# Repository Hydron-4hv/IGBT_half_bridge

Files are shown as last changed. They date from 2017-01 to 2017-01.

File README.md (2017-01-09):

# IGBT_half_bridge
PCB for general use of TO-247 IGBTs in half bridge configuration. Variants for parallel IGBTs and horizontal mounting

Design notes:
- Have included a lot of different holes for various mounting requirements, so looks a bit swiss-cheesed
- Should be able to trim off part of the board and still access Vbus+/- and bridge output nodes
- Electrolytic cap footprints should be able to accommodate up to 35mm dia. caps, though with a little bit hanging over the edge of the PCB
- Various Fischer Elektronik SK 481 heatsinks can be used (with clips to hold IGBTs), either 2 separate heatsinks (suggest 37.5mm length) to avoid isolation requirements, or larger 50-84mm with isolation pads behind IGBTs. In all cases use an insulated washer for heatsink mounting screw, and consider adding kapton tape or similar to top layer to add isolation between heatsink and top layer tracks.
- Other heatsinks with IGBTs either vertical or horizontal (under PCB mount, screws accessed via supplied holes) can be used as desired 

Output notes:
- 3 different "PCB Variants" have been defined and output files generated:
  - Single IGBT in each of upper and lower half bridge position, SMD gate resistor, 2x 37.5mm SK481 heatsinks, no electrolytic caps
  - Dual IGBTs in each of upper and lower half bridge position, THD gate resistor, 2x 37.5mm SK481 heatsinks, electrolytic caps fitted
  - Dual IGBTs in each of upper and lower half bridge position (horizontally mounted), THD gate resistor, no heatsink, electrolytic caps fitted
- The "schematic" PDFs include a 3D model for viewing in compatible software (Adobe reader works, Foxit does not, unsure about others)

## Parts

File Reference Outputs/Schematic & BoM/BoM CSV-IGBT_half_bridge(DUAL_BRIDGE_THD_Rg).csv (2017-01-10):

Designator | Value | Description | Fitted | Footprint | LibRef | Quantity
C1 | 5uF 800V | Capacitor | Fitted | B32774 5uF 800V | Cap | 1
C2, C3 | 390uF | WCAP-AIG8 Aluminum Electrolytic Capacitors, 390uF | Fitted | WCAP-AIG8_30x46 | WCAP-AIG8, 861011485019 | 2
C4, C5, C6, C7, C8, HS1, HS2 |  |  | Fitted | 2220C, 1812C, 2220C, 1812C, Cap_multi_footprint, SK 481 37.5, SK 481 37.5_FLIP | Capacitor, Capacitor, Capacitor, Capacitor, Capacitor, SK_481_37.5, SK_481_37.5 | 7
D1, D3, D5, D7 |  | SS26 Schottky rectifier | Fitted | DO-214AA_(SMB-J-BEND)_UNI | SS26 | 4
D2, D4, D6, D8 |  | WE-TVSP Power TVS Diode, bidirectional, 600 W, 24 VDC | Fitted | DO-214AA_Bidirectional | WE-TVSP DO-214AA, 824521241 | 4
J1 |  | WR-BHD 2.54mm Male Box Header | Fitted | 61202021621 | 61202021621 | 1
L1, L2, L3, L4 | 32O | WE-CBF SMD EMI Suppression Ferrite Bead, 1206, 32O | Fitted | WE-CBF_1206_High Speed | WE-CBF, 7427921 | 4
Q1, Q2, Q3, Q4 |  | IGBT, TO-247, Vertical | Fitted | TO-247 | TO-247_IGBT_V | 4
R1, R2, R13, R18 | 3R3 2W | Resistor | Fitted | Res_Radial_2W | Res2 | 4
R3, R4, R7, R8, R11, R12, R16, R17 | 5R6 1W | Resistor | Not Fitted | RES_2512 | Res2 | 0

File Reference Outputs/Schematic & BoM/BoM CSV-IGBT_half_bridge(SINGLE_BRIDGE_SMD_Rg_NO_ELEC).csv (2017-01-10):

Designator | Value | Description | Fitted | Footprint | LibRef | Quantity
C1 | 5uF 800V | Capacitor | Fitted | B32774 5uF 800V | Cap | 1
C2, C3 | 390uF | WCAP-AIG8 Aluminum Electrolytic Capacitors, 390uF | Not Fitted | WCAP-AIG8_30x46 | WCAP-AIG8, 861011485019 | 0
C4, C6, HS1, HS2 |  |  | Fitted | 2220C, 2220C, SK 481 37.5, SK 481 37.5_FLIP | Capacitor, Capacitor, SK_481_37.5, SK_481_37.5 | 4
C5, C7, C8 |  |  | Not Fitted | 1812C, 1812C, Cap_multi_footprint | Capacitor | 0
D1, D3 |  | SS26 Schottky rectifier | Fitted | DO-214AA_(SMB-J-BEND)_UNI | SS26 | 2
D2, D4 |  | WE-TVSP Power TVS Diode, bidirectional, 600 W, 24 VDC | Fitted | DO-214AA_Bidirectional | WE-TVSP DO-214AA, 824521241 | 2
D5, D7 |  | SS26 Schottky rectifier | Not Fitted | DO-214AA_(SMB-J-BEND)_UNI | SS26 | 0
D6, D8 |  | WE-TVSP Power TVS Diode, bidirectional, 600 W, 24 VDC | Not Fitted | DO-214AA_Bidirectional | WE-TVSP DO-214AA, 824521241 | 0
J1 |  | WR-BHD 2.54mm Male Box Header | Fitted | 61202021621 | 61202021621 | 1
L1, L2 | 32O | WE-CBF SMD EMI Suppression Ferrite Bead, 1206, 32O | Fitted | WE-CBF_1206_High Speed | WE-CBF, 7427921 | 2
L3, L4 | 32O | WE-CBF SMD EMI Suppression Ferrite Bead, 1206, 32O | Not Fitted | WE-CBF_1206_High Speed | WE-CBF, 7427921 | 0
Q1, Q2 |  | IGBT, TO-247, Vertical | Fitted | TO-247 | TO-247_IGBT_V | 2
Q3, Q4 |  | IGBT, TO-247, Vertical | Not Fitted | TO-247 | TO-247_IGBT_V | 0
R1, R2, R13, R18 | 3R3 2W | Resistor | Not Fitted | Res_Radial_2W | Res2 | 0
R3, R4, R7, R8 | 5R6 1W | Resistor | Fitted | RES_2512 | Res2 | 4
R11, R12, R16, R17 | 5R6 1W | Resistor | Not Fitted | RES_2512 | Res2 | 0

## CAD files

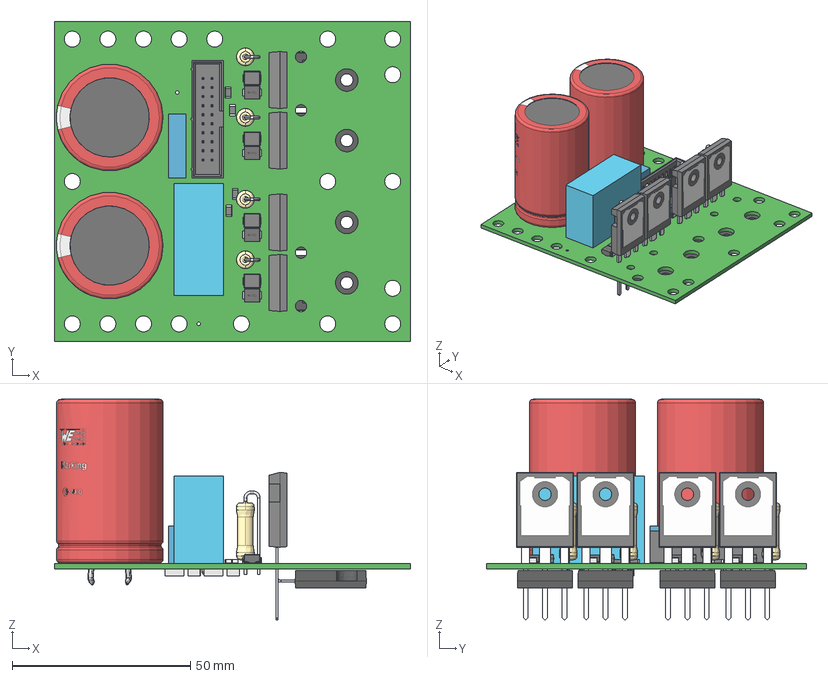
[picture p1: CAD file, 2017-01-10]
Reference Outputs/Mechanical/Export STEP Model of complete PCB_IGBT_half_bridge-(DUAL_BRIDGE_THD_Rg_HORIZONTAL_IGBT).step
100.0 x 90.0 x 61.9 mm
BoardIGBT_half_bridge
L\X2\00F6\X0\tende x 8
Extruded x 2
User_Library-TO-247_CASE_340L-02_Vertical_1 x 4
User_Library-TO-247_CASE_340L-02_Vertical_2 x 4
User_Library-TO-247_CASE_340L-02_Vertical_3 x 4
User_Library-TO-247_CASE_340L-02_Vertical_4 x 4
Open_CASCADE_STEP_translator_6.8_3.1.1 x 4
Lead x 8
DO-214AA_Bidirectional x 4
User_Library-RESAD375W80L1600D500_2W_Body x 4
User_Library-RESAD375W80L1600D500_2W_Lead x 4
6120xx21621_PIN x 20
User_Library-TO-247H x 4
30x46 x 2
Open_CASCADE_STEP_translator_6.8_6.1.1 x 2
Open_CASCADE_STEP_translator_6.8_6.1.2 x 2
Open_CASCADE_STEP_translator_6.8_6.2.1 x 2
Open_CASCADE_STEP_translator_6.8_4.1.1 x 2
Open_CASCADE_STEP_translator_6.8_4.1.2 x 2
Open_CASCADE_STEP_translator_6.8_4.2.1 x 2

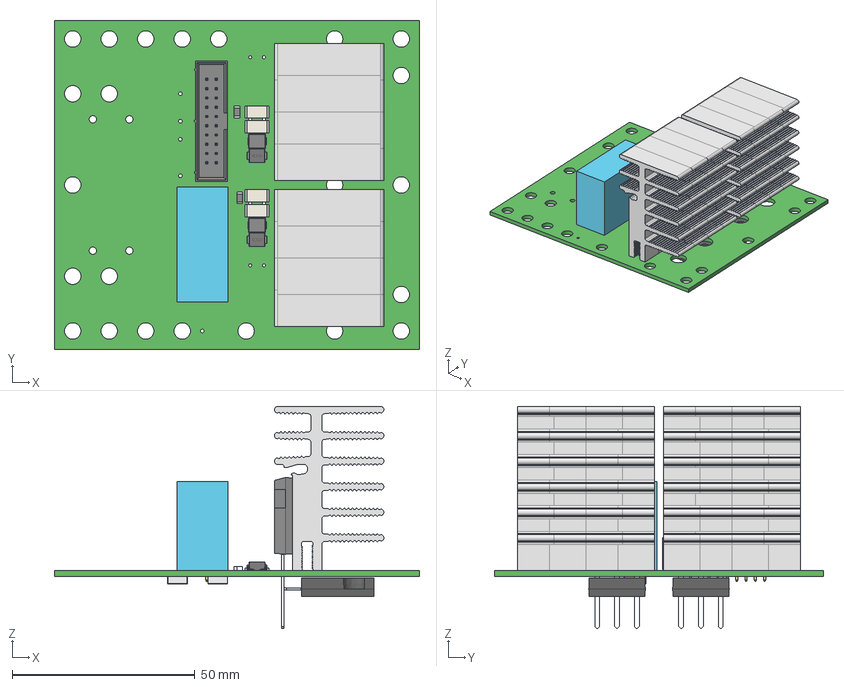
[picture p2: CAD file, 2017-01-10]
Reference Outputs/Mechanical/Export STEP Model of complete PCB_IGBT_half_bridge-(SINGLE_BRIDGE_SMD_Rg_NO_ELEC).step
100.0 x 90.0 x 60.9 mm
BoardIGBT_half_bridge
L\X2\00F6\X0\tende x 4
Extruded x 13
User_Library-TO-247_CASE_340L-02_Vertical_1 x 2
User_Library-TO-247_CASE_340L-02_Vertical_2 x 2
User_Library-TO-247_CASE_340L-02_Vertical_3 x 2
User_Library-TO-247_CASE_340L-02_Vertical_4 x 2
Open_CASCADE_STEP_translator_6.8_3.1.1 x 2
Lead x 4
DO-214AA_Bidirectional x 2
sk481 x 8
6120xx21621_PIN x 20
User_Library-TO-247H x 2
Open_CASCADE_STEP_translator_6.8_6.1.1 x 2
Open_CASCADE_STEP_translator_6.8_6.1.2 x 2
Open_CASCADE_STEP_translator_6.8_6.2.1 x 2

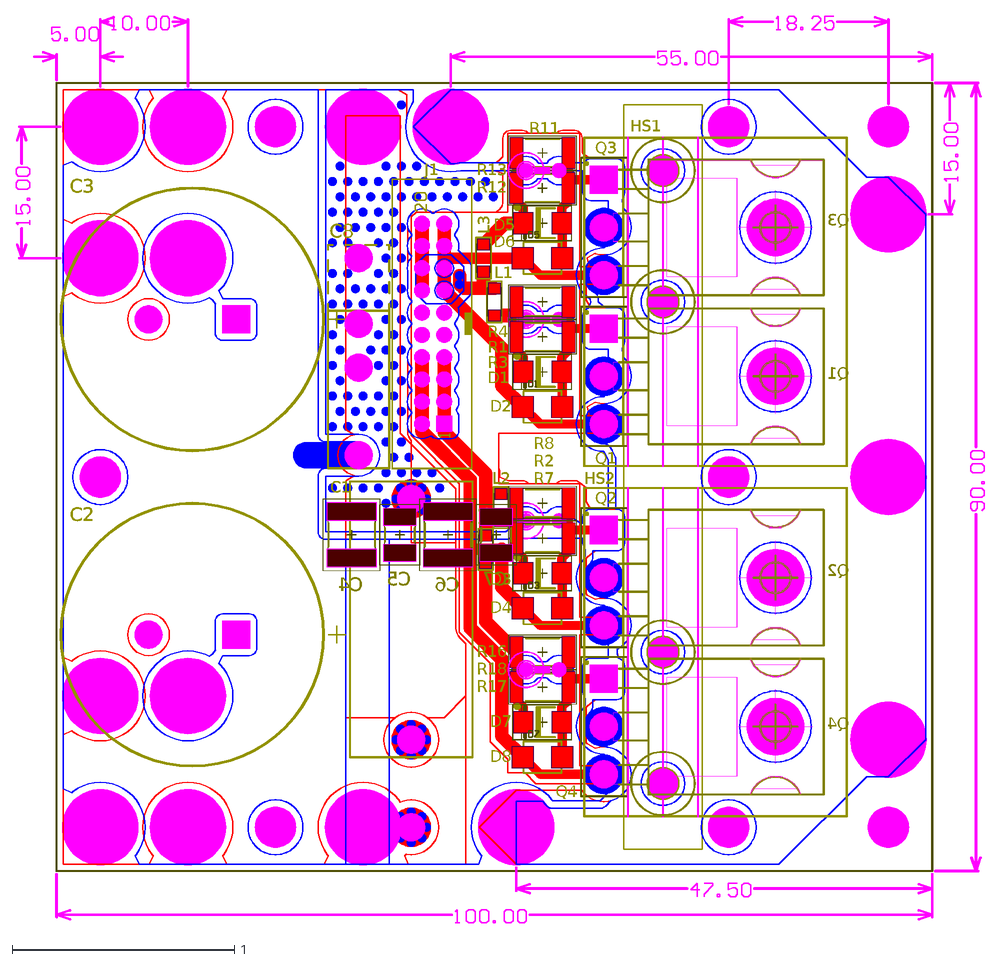
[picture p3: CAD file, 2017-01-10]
Reference Outputs/Mechanical/IGBT_half_bridge.DXF
L4
L3
L2
L1
C1
Q2
Q1
D1
D2
D3
D4
R2
Q3
Q4
R1
D5
D6
D7
D8
HS1
HS2
R3
R4
R7
R8
R11
R12
R13
R16
R17
R18
J1
C2
C3
C4
C5
C6
C7
C8

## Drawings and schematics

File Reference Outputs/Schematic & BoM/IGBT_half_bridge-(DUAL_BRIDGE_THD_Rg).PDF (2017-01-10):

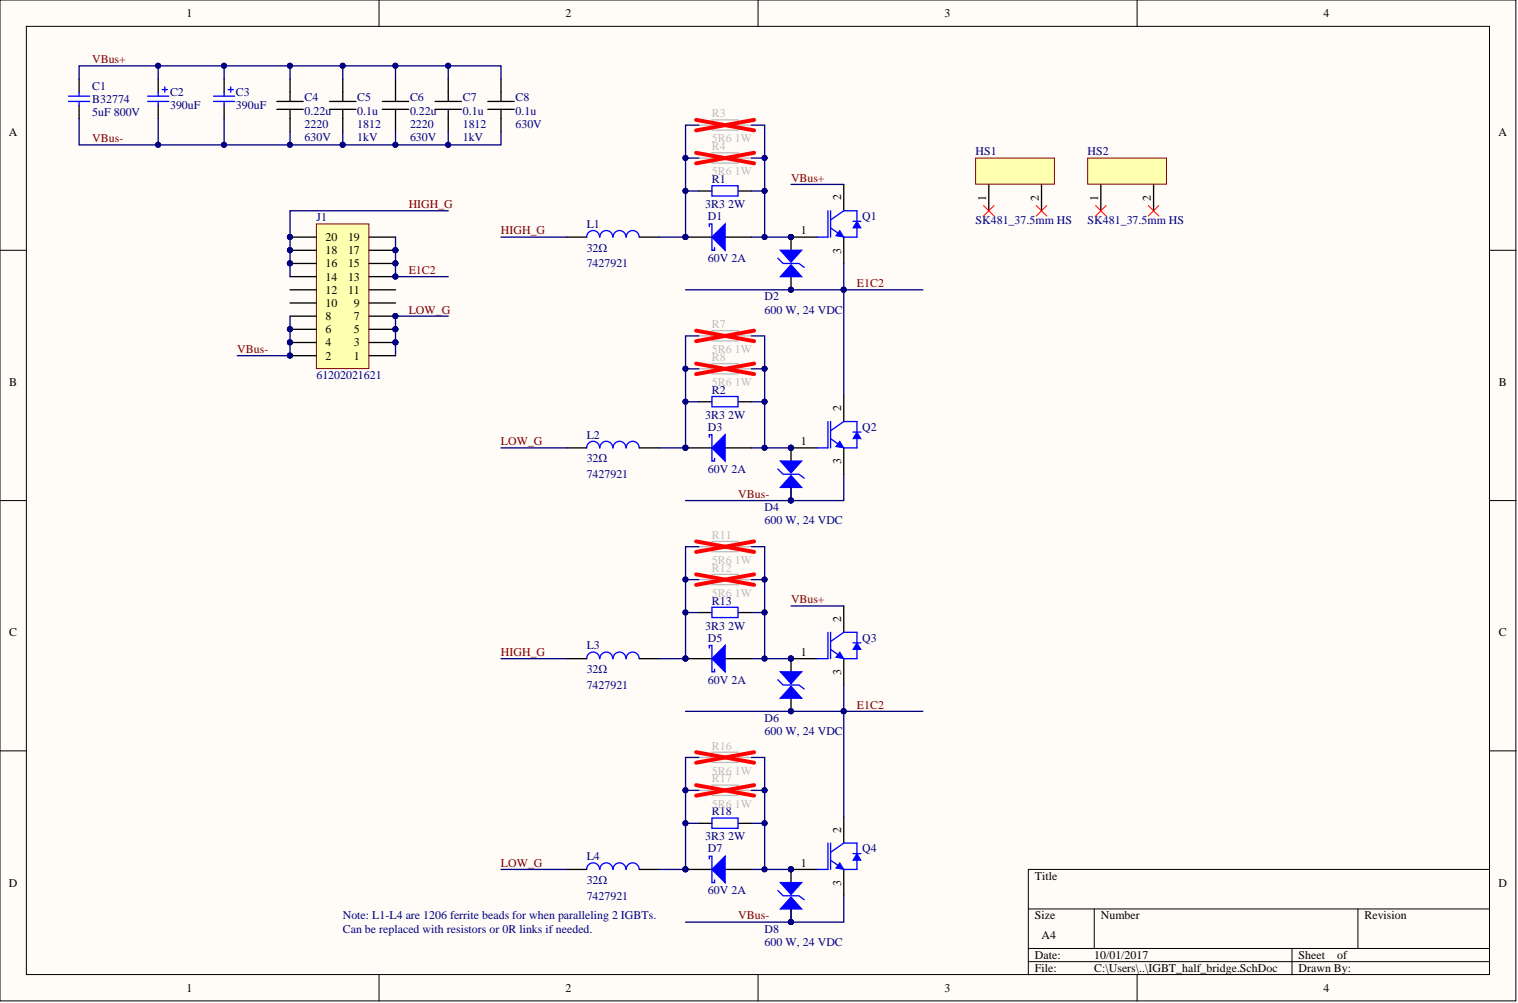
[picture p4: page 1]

Note: L1-L4 are 1206 ferrite beads for when paralleling 2 IGBTs.
Can be replaced with resistors or 0R links if needed.

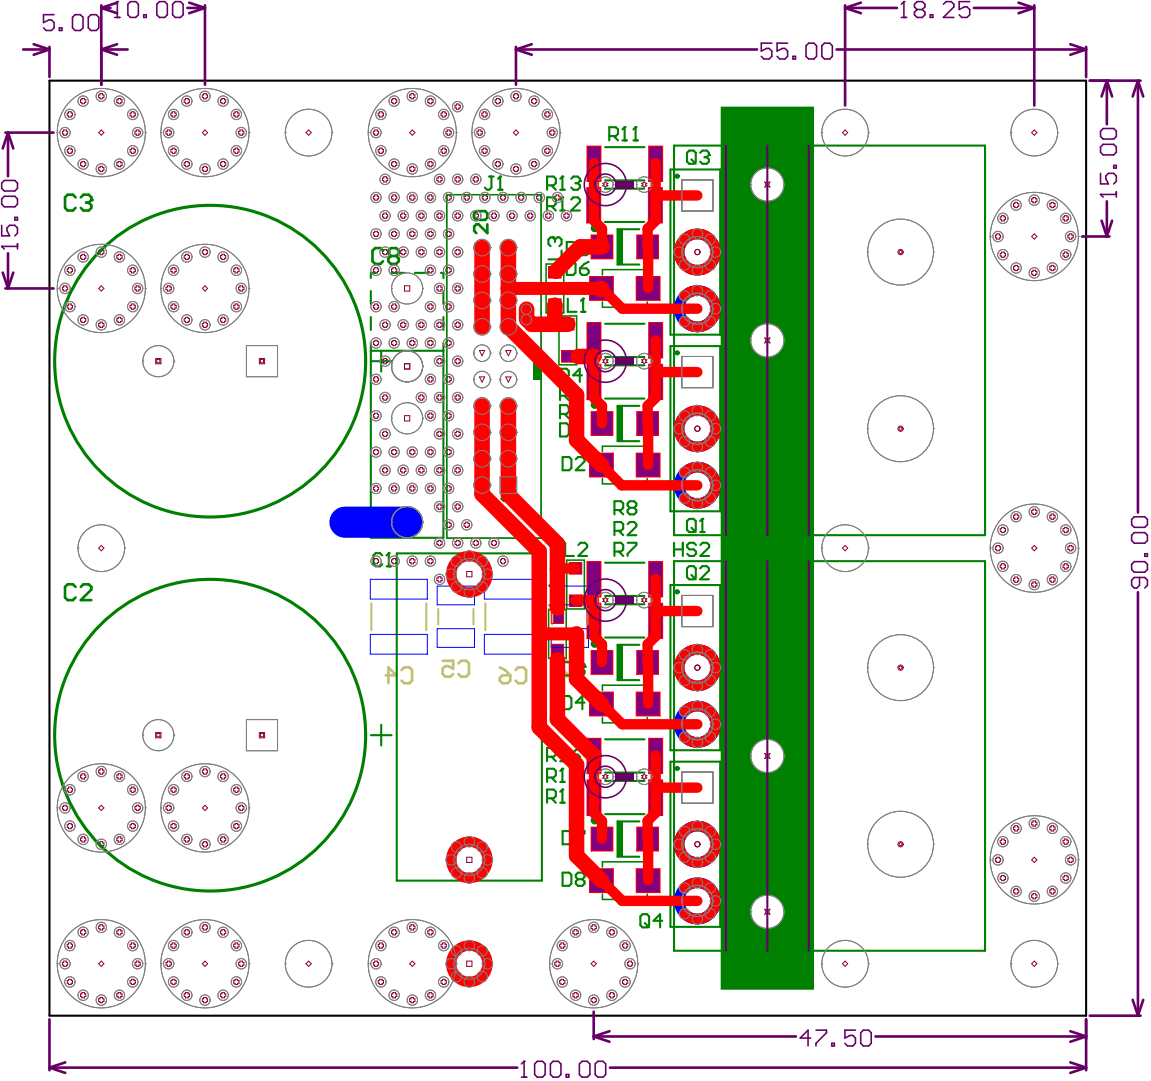
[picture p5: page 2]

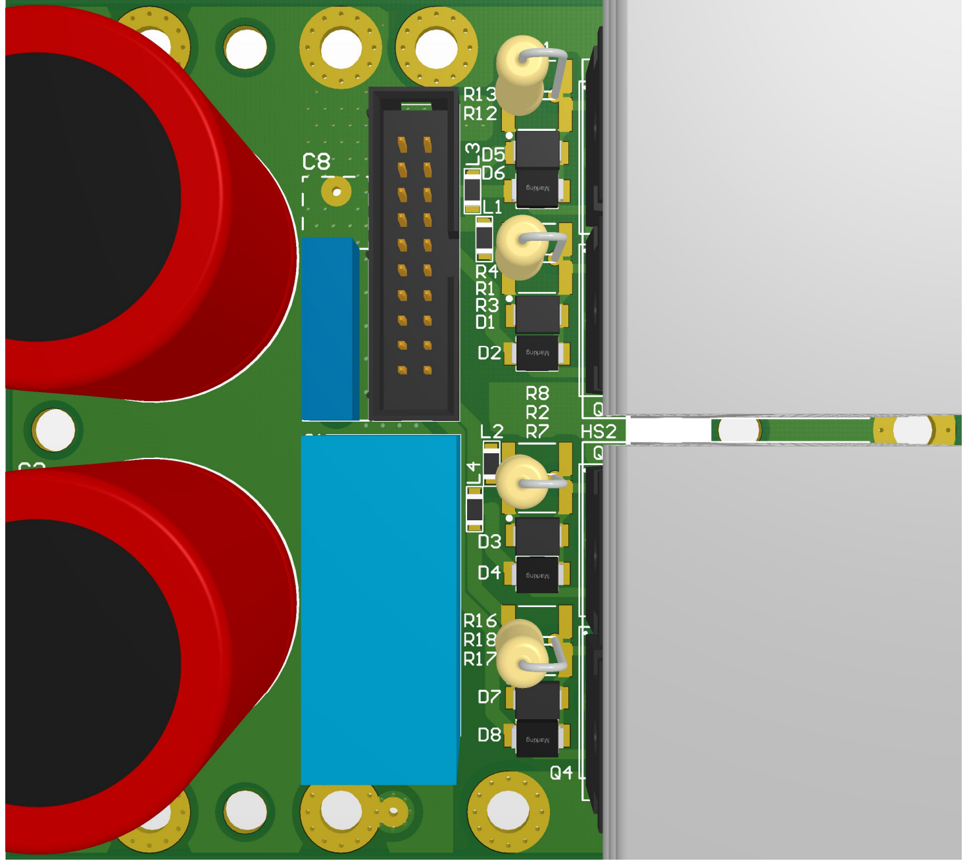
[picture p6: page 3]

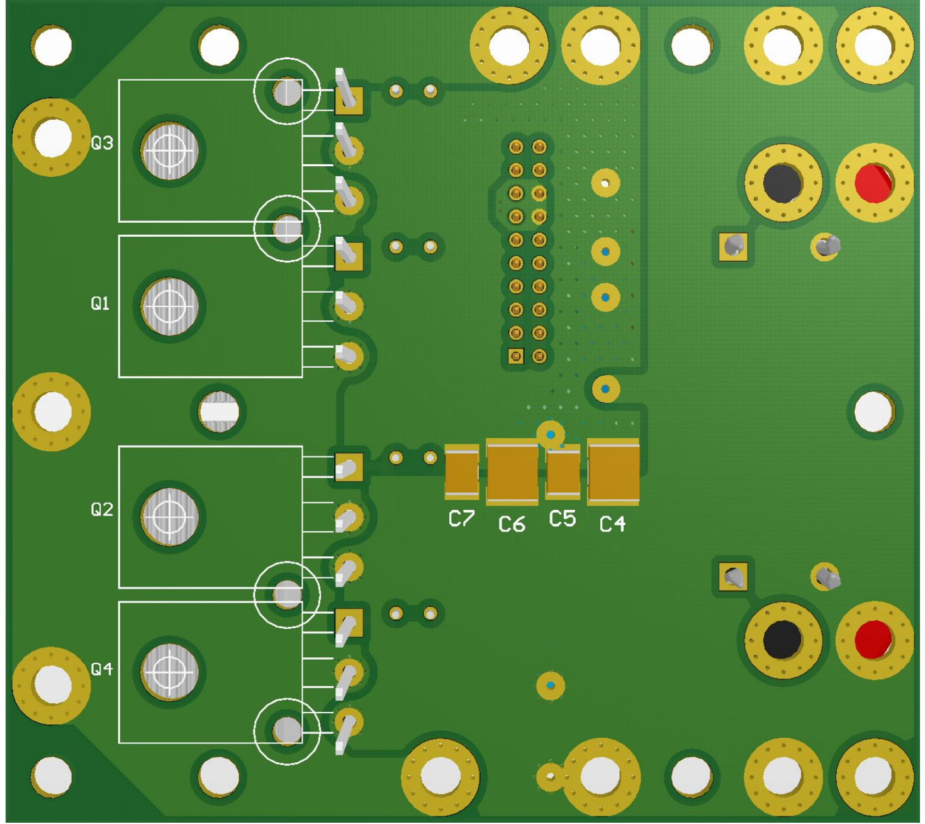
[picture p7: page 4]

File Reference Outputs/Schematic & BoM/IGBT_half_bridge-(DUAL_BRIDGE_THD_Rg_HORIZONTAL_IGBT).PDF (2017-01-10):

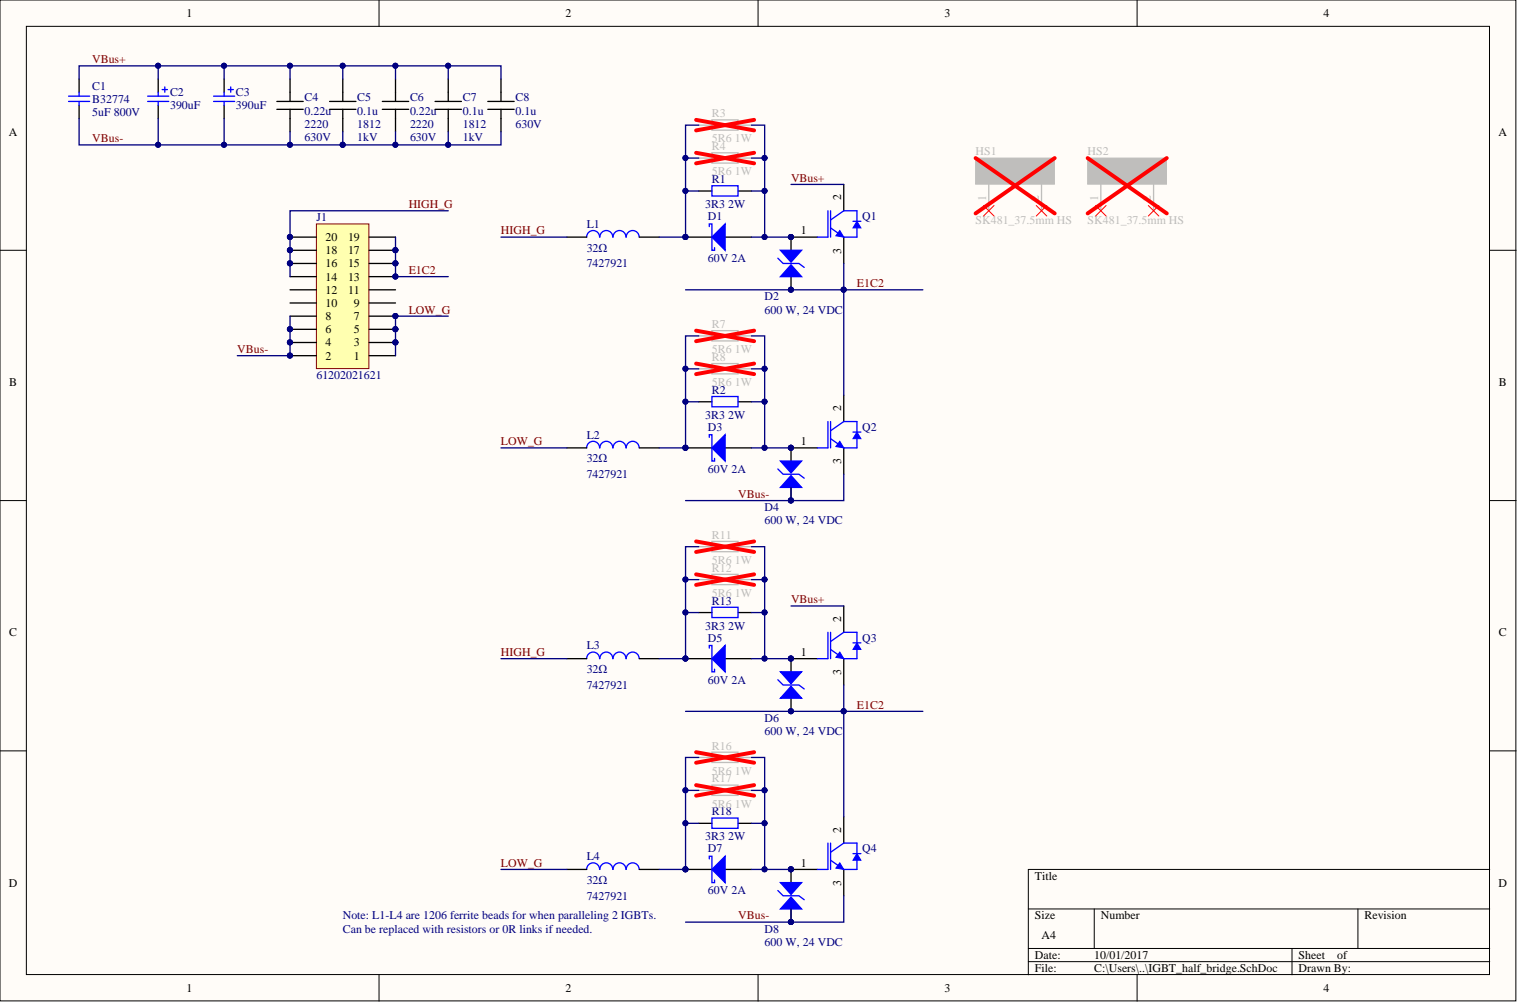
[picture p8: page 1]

Note: L1-L4 are 1206 ferrite beads for when paralleling 2 IGBTs.
Can be replaced with resistors or 0R links if needed.


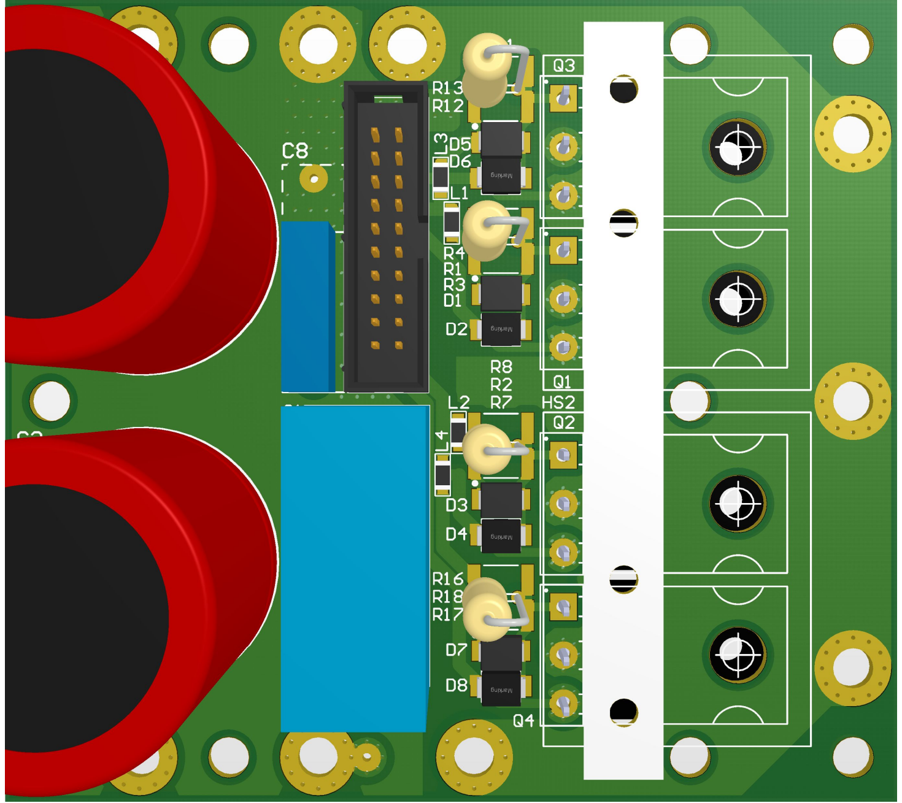
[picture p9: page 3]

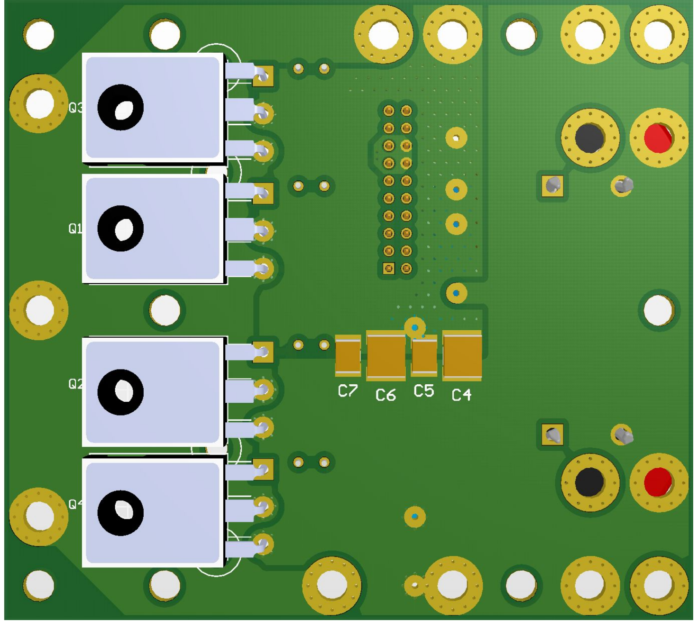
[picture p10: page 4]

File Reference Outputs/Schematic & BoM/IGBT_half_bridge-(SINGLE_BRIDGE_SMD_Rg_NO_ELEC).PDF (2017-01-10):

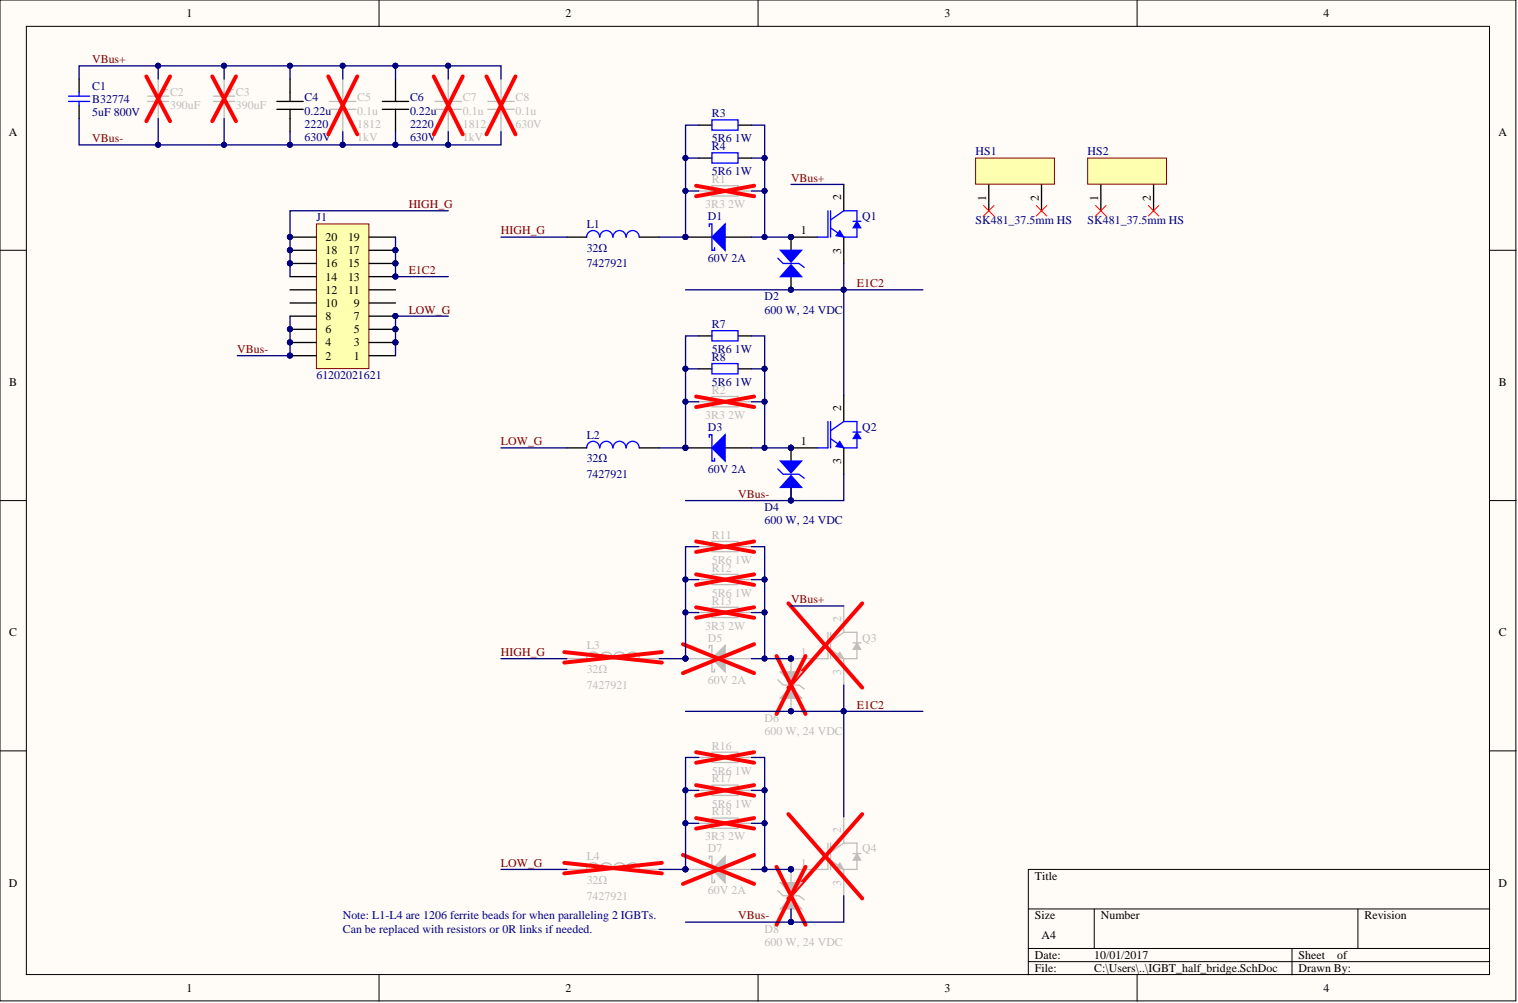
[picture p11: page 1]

Note: L1-L4 are 1206 ferrite beads for when paralleling 2 IGBTs.
Can be replaced with resistors or 0R links if needed.


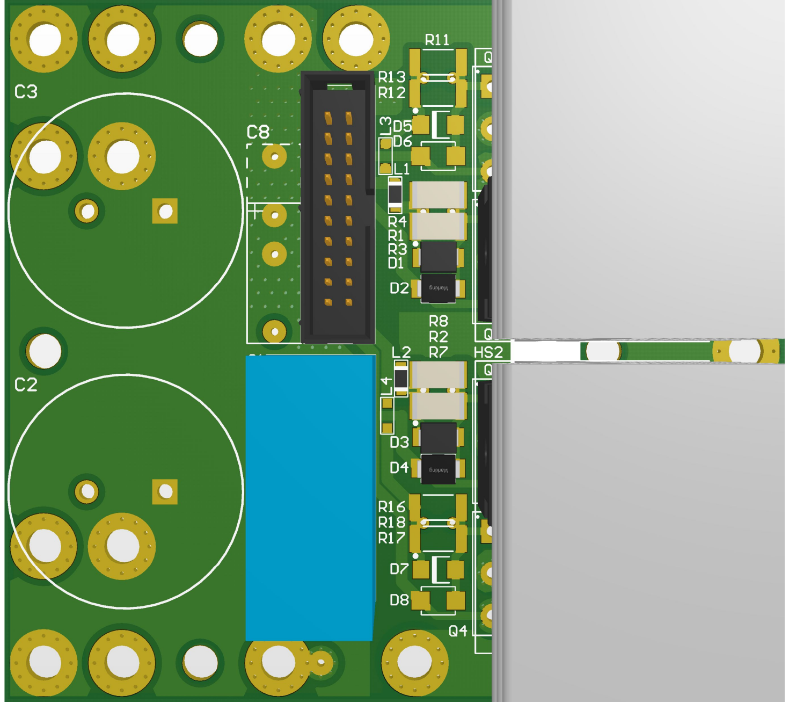
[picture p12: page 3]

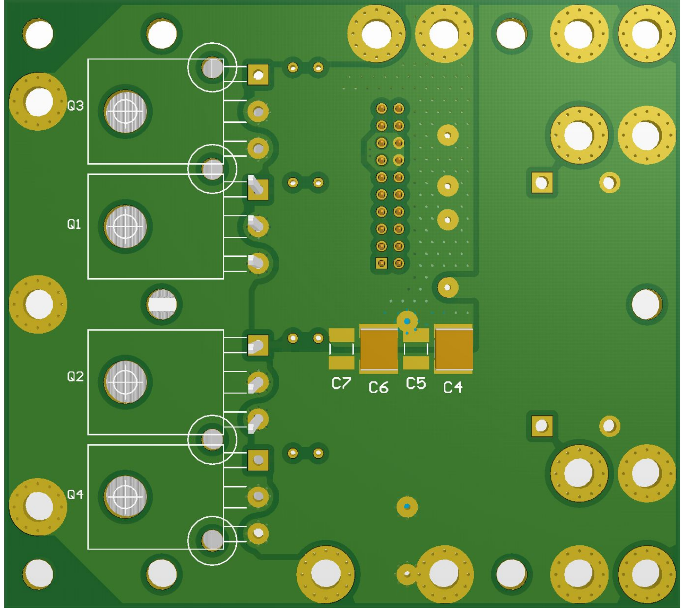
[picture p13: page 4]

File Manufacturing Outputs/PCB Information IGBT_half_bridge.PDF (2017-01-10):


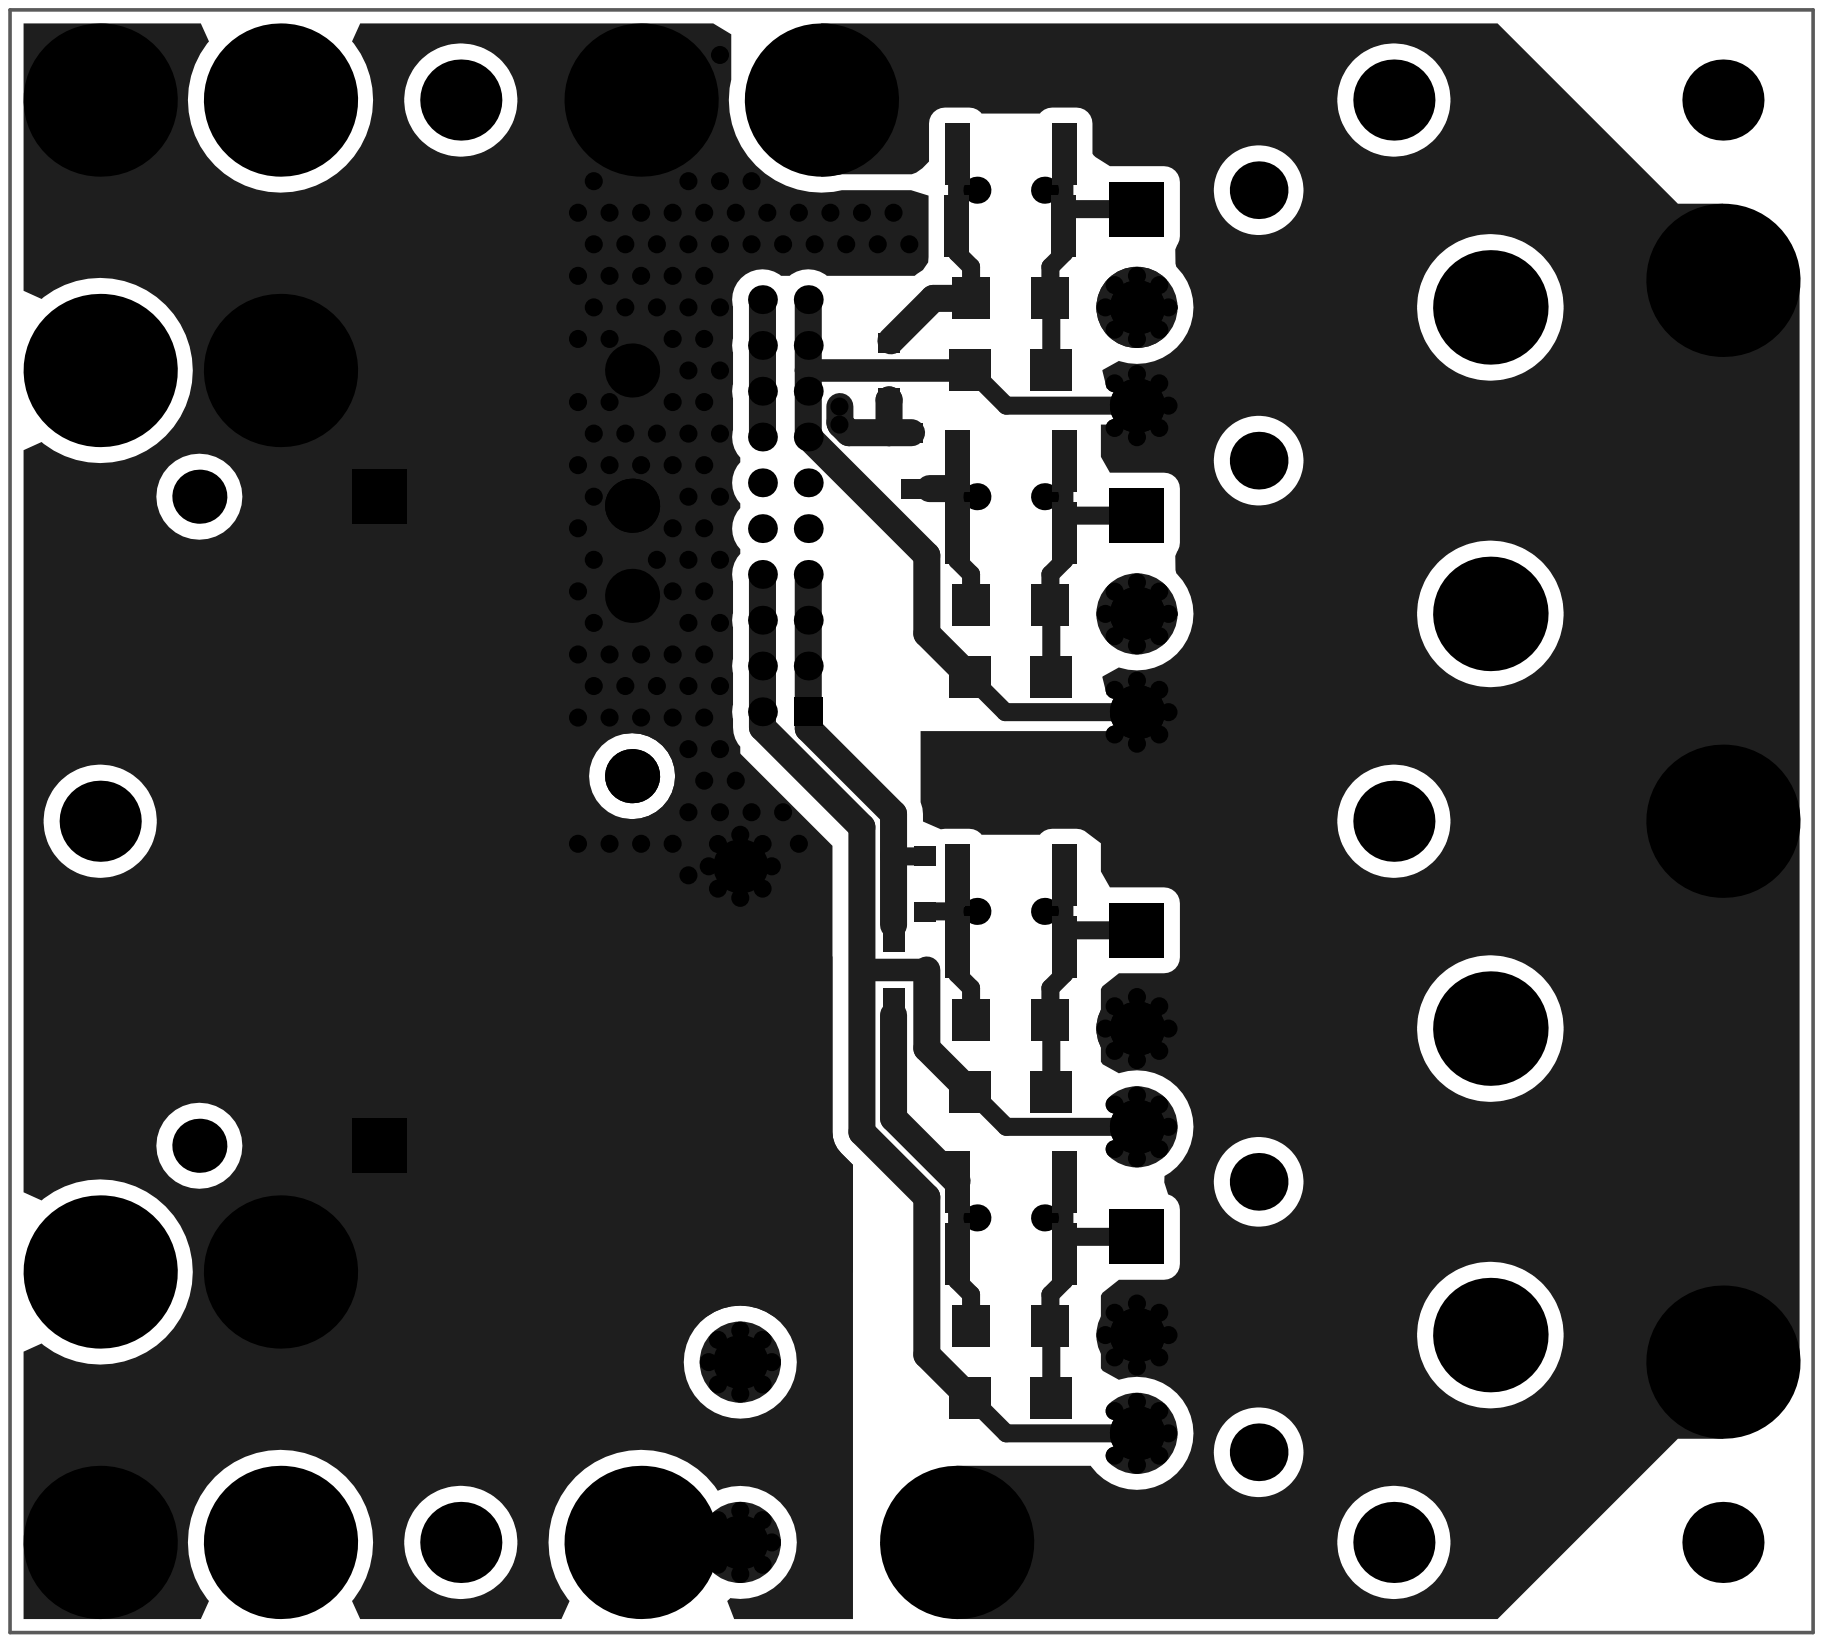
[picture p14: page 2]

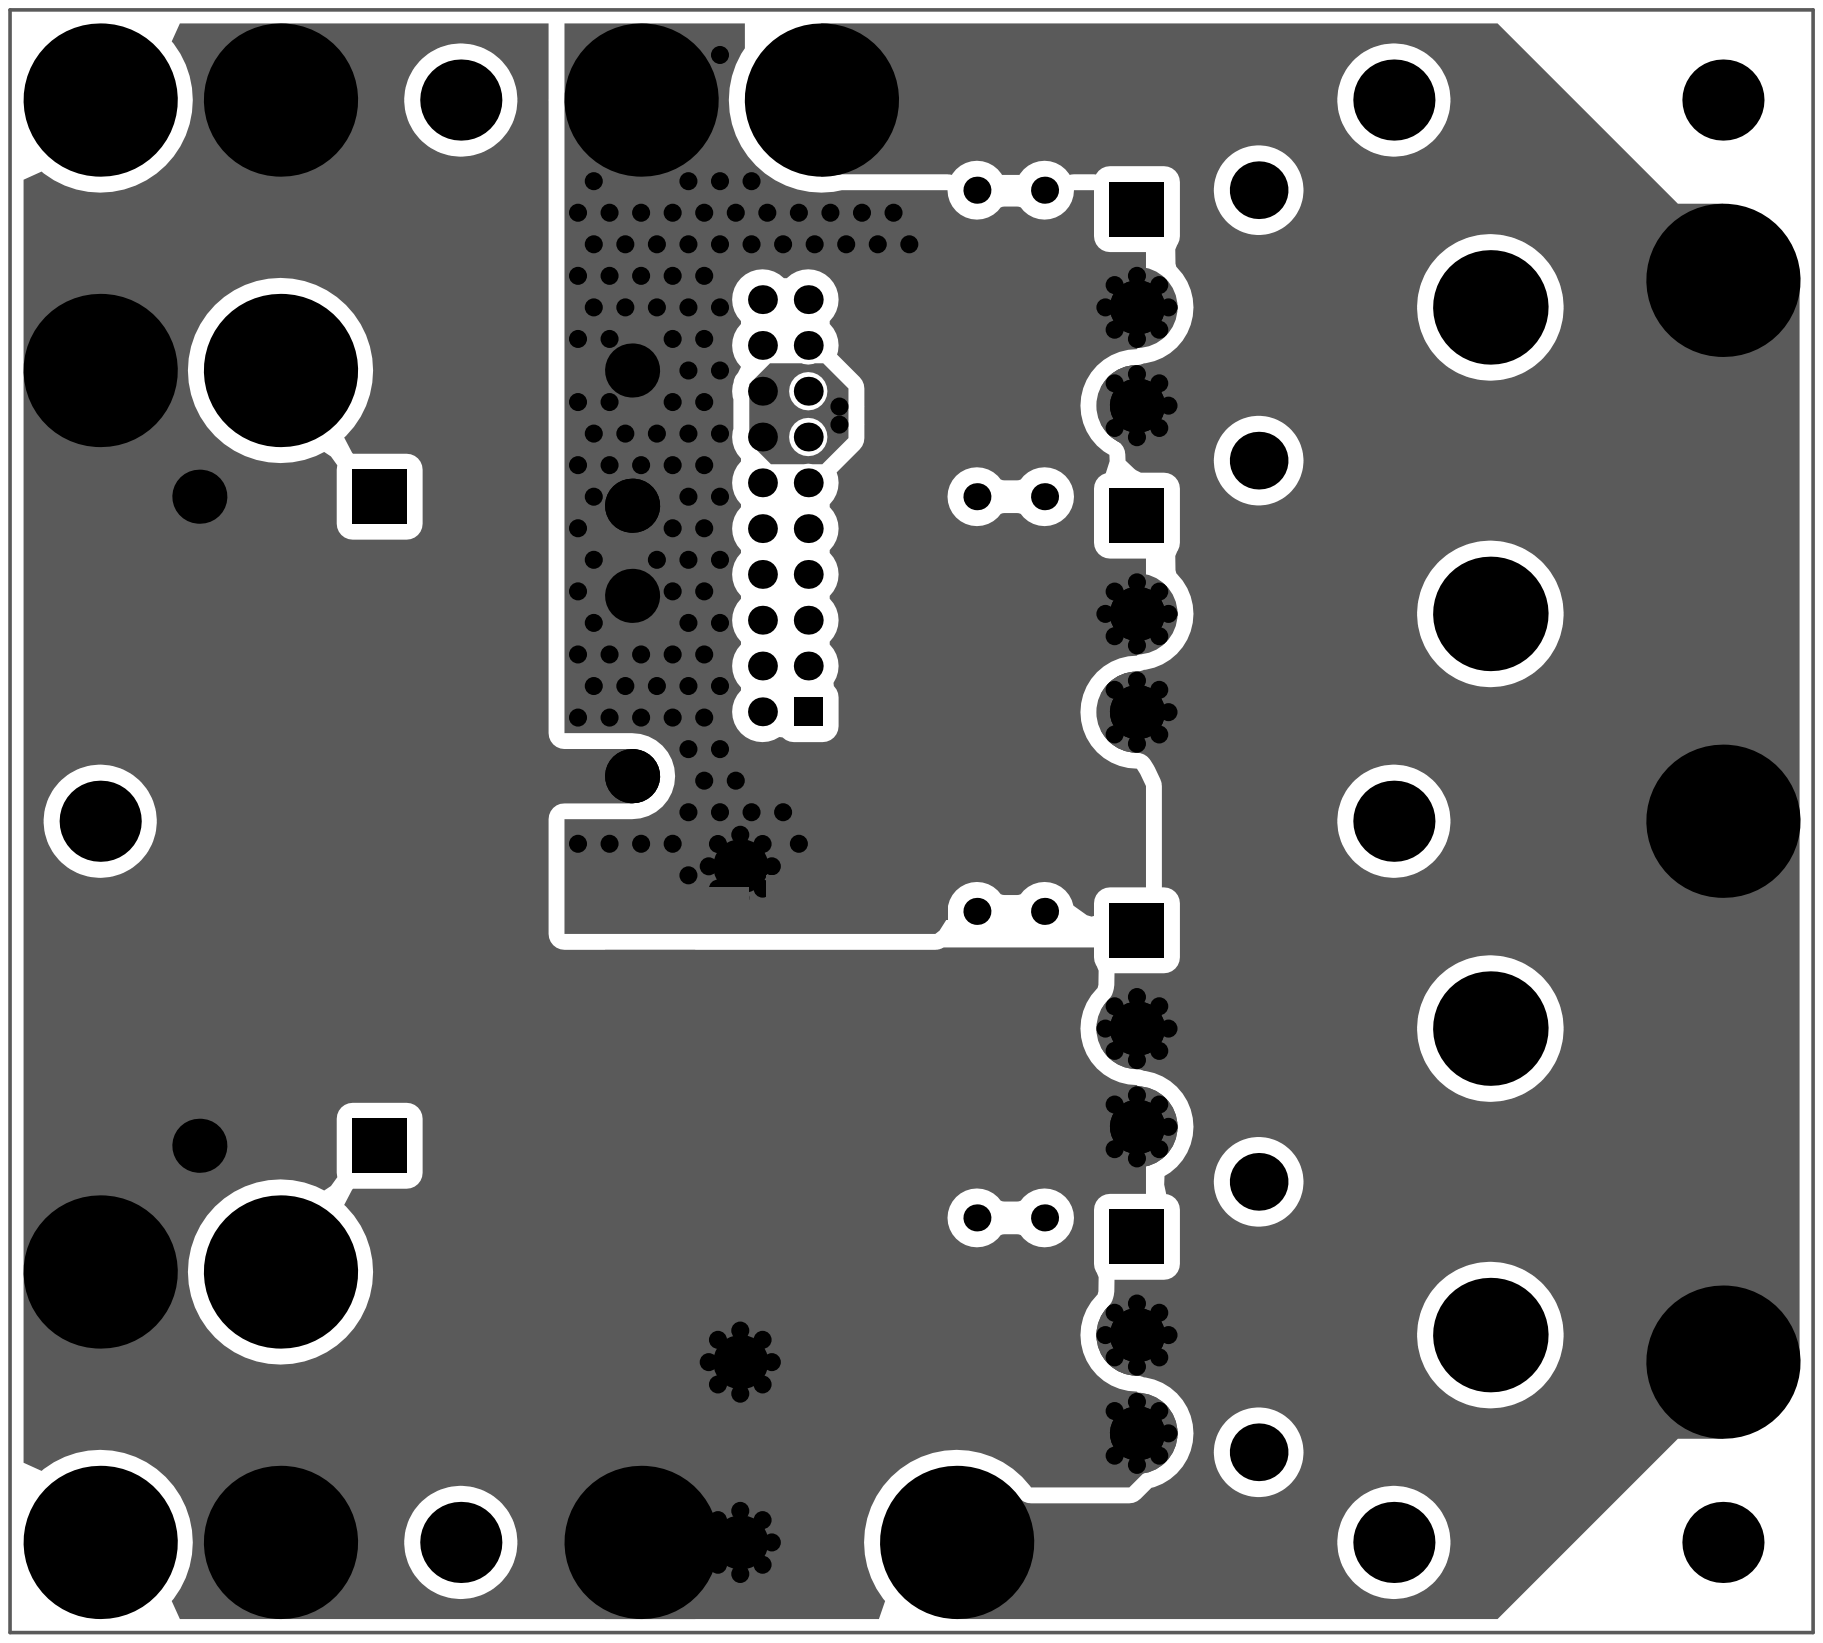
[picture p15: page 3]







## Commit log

2017-01-09 Update README.md
    Add description of PCB, variants
2017-01-09 Add files via upload
    Add design files
    [IGBT_half_bridge.PcbDoc, IGBT_half_bridge.PrjPcb, IGBT_half_bridge.SchDoc]
2017-01-09 Add files via upload
    Add manufacturing and reference outputs
    [BoM CSV-IGBT_half_bridge(DUAL_BRIDGE_THD_Rg).csv, BoM CSV-IGBT_half_bridge(DUAL_BRIDGE_THD_Rg_HORIZONTAL_IGBT).csv, BoM CSV-IGBT_half_bridge(SINGLE_BRIDGE_SMD_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]
2017-01-09 Add files via upload
    Updated PDF output to show individual PCB layers
2017-01-09 Add files via upload
    Update with individual PCB layers in PDF
2017-01-10 Add files via upload
    Add decoupling capacitors, fix missing footprints, increase creepage distances
    [BoM CSV-IGBT_half_bridge(DUAL_BRIDGE_THD_Rg).csv, BoM CSV-IGBT_half_bridge(DUAL_BRIDGE_THD_Rg_HORIZONTAL_IGBT).csv, BoM CSV-IGBT_half_bridge(SINGLE_BRIDGE_SMD_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]
2017-01-10 Delete IGBT_half_bridge-Plated.TXT
    remove old data
